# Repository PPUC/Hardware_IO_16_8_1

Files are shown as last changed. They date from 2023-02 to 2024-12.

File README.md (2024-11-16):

# Standard IO PCB for PPUC Project
This is the hardware for a standard IO card which was designed for the PPUC pinball project, but can be useful in other applications as well.
It is designed for being low cost and functional for experimental use.  
Not everything is tested nor does it fulfill EMC or any other specifications.  
Use at your own risk!
To make use of anything of this project a basic understanding of electronics and programming is necessary. Nothing of it is "plug and play". I'm surely not liable for any damage to assemblies, pinball machines or even persons.

## Picture of the Board
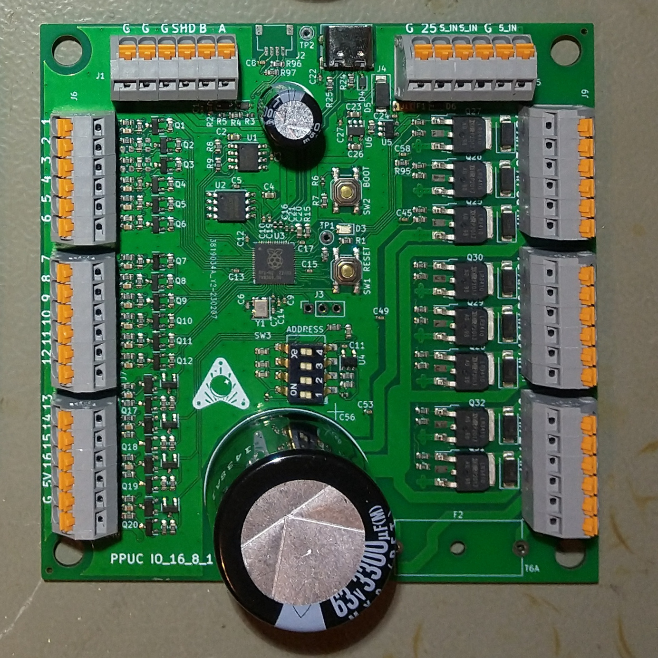
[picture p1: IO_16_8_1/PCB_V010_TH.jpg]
PCB Pic


## Name
IO_16_8_1 as it has 16 inputs, 8 outputs and one special output.  
Actually the inputs can also be used as outputs (see later in this document).

## Power Supply
The IO card must be supplied by 5 V (+-0.5 V) for logic and inputs. Additionally nominal 48 V for high power outputs. As these outputs are open drain, the voltage can actually be up to 60 V. In the circuit diagram the voltage is called 48 V.

## Controller
A RP2040 is used for it's cost/performance ratio. It is the same controller that is used in the Raspberry Pi Pico.

## Communication Interfaces
* RS_485: main communication interface for controlling outputs and scan inputs. Usually connected to a host interface like a PC or Raspberry Pi or similar.
* USB C: for programming, debug and flashing
* Serial Wire: alternative for programming, debug and flashing
* IIC: the PCB can be populated with an QWIIC connector (normally not mounted). This can be used for connecting to other PCBs or experimental use. It uses the same UART as for the RS485.
* UART, I2C, SPI: instead of using the input pins for inputs they can also be used as an additional interface (see docu of RP2040 for pins and function). Speed up to 10 kHz should be possible (100 kHz for In_2 and In_3).

## Switches (on board)
* Reset: hardware reset for controller (RP2040)
* Boot: if active the board connects to a PC like an USB stick. Usually used for programming the code into the flash memory on the board.
* DIP-switches: usually used to select an address for RS485 (16 combinations)

## Inputs (and low power outputs)
The 16 inputs are used for reading the state of an external switch. The switch is normally connected to ground (GND). Internally the input is pulled up to 5 V by a 10k resistor.

All inputs can also be used as signal-outputs (if programmed accordingly). The output is internally pulled up by a 10k resistor to 5 V. A higher voltage can be applied externally (max. 30 V) but be sure to have your hardware and software! setup correctly as no protection for damage is provided in that case. A maximum of 2 mA can be sinked/sourced.

The inputs In_2 and In_3 are designed for higher speed (100 kHz). The Pull-Up can be soldered to other pads to be pulled to 3,3 V (instead of 5 V). An input capacitance can be added (soldered) for better noise immunity but lower speed. Since version 1.0.1 the caps are soldered by default and must be removed if a high-speed serial connection is needed.

The input terminals can also be "miss"used for a switch matrix. To do that (no matter if used as coloum or row) the input resistor (330 Ohm) must be short cut (or replaced by a zero Ohm type). Background: the 330 Ohm resistor protects the circuit if the terminal is used as an output and accidently a short cut is done at the terminal. Unfortunately the low voltage value gets too high when used in a switch matrix (diode voltage plus voltage drop due to added up currents through the resistor). This happens when more switches are closed at the same time. Instead you could also use the specially designed PCB "Hardware_IO_16x8_matrix" for your switch matrix.

The inputs In_13 to In_16 have an additional open drain output transistor that allows higher currents in case of being used as an output (up to 3 A at 25 °C ambient temperature). The outputs are internally pulled up by a 10k resistor to 5 V. A higher voltage (max. 30 V) can be applied externally but be sure to have your hardware and software! setup correctly as no protection for damage is provided in that case. Please be aware that the default state (before software takes over control) is "on". 
If used as input In_13 to In_16 feature a memory (similar to a relay self-holding function). If the input has ever seen a low signal (e.g. switch closed to GND) it will stay that way until it gets an active high signal from the RP2040 (make the corresponding pin an output with signal "high" and then make it an input again). If this behavior is not wanted you can lift pin 3 of Q13 to Q16, then you have an input/output like e.g. terminal 1 with static behavior but no additional output power.

## High Power Outputs
There are 8 high power outputs available. Usually they are connected to pinball solenoids or flashers. A recovery diode for the solenoids is placed on the pcb, so no need for diodes at the coils. The outputs are open drain and drive currents up to 20 A with a load connected to a voltage of up to 60 V. Be aware that the current is limited by the fuse F2. It will blow within about 1 s at 20 A. You might use a 10 A fuse if necessary.

It's recommended to use 2 wires (back and forth) for each solenoid. That improves the EMC a lot.

## Special Output
One special output is available for high speed signals. The voltage is 5 V, it is a push pull output that can drive a current up to 8 mA. It can be used to e.g. control a WS2812 LED strip.

## Recommendations
* Connect only one Flipper to a pcb if possible. The advantage is, that all the energy of the big capacitor is available for the flipper, which is usually the solenoid with the highest current. If you have more flipper fingers than PCBs then spread the flipper solenoids as even as possible across the PCBs (e.g. if you have 6 flipper fingers it's better to connect 2 per board instead of all 6 at one board).
* Wire related switches and solenoids for fast flip devices (e.g. flipper, bumper, sling, kick back) to the same pcb. Then you can archive the shortest possible time lag between activating the switch and firing the solenoid.
* RS485 termination: short JP2 at the end of the RS485 bus. There should also be a 120 Ohm resistor at the beginning of the bus (e.g. USB to RS485 adapter).
* RS485 biasing: short JP1 and JP3 exactly once at any point of the RS485 bus. Only do this if no resistors are installed on the USB to RS485 adapter. 
* It's recommended to use flipper coils for higher voltage (like 40 - 50 V) as they draw less current. Since Version 1.1.1 low resistance coils (designed for 24 V) should work as well. You should also change the fuse F2 to 10 A for that application.
* If the MOSFETs on the high power outputs are not available (or you want to use the big player brands) here are some alternatives (I haven't tested any of them, but they should work according to their specification): GL40N10A4 (seems to be the same as NCE0140KA), RD3P200SNFRA, NVD6824NL, IPD90N10S4L-06, LSGG10R085W3

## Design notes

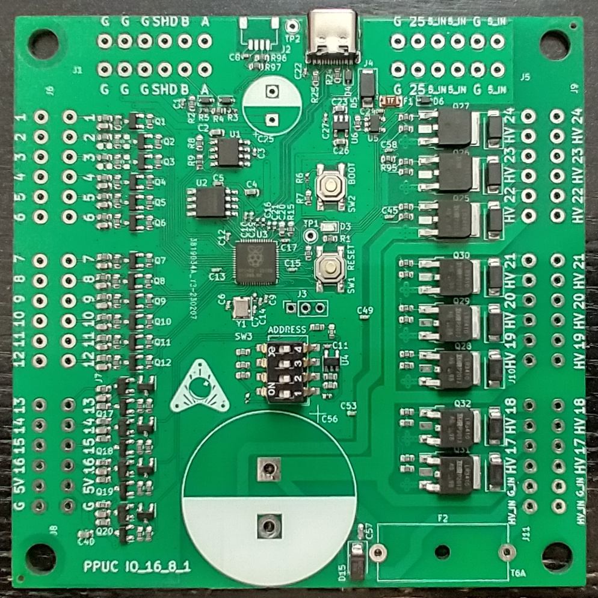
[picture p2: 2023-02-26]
IO_16_8_1/PCB_V010_SMD.jpg

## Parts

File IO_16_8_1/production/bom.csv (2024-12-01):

Designator | Footprint | Quantity | Value | LCSC Part #
C1, C10, C11, C12, C13, C14, C15, C17, C19, C22, C24, C27, C3, C45, C49, C5, C53, C58, C8, C9 | 0402 | 20 | 100n
C16, C21 | 0402 | 2 | 1u
C2, C20, C23, C26, C4, C40 | 0603 | 6 | 10u
C25 | CP_Elec_6.3x5.4 | 1 | 100µ 16V
C28, C29, C30, C31, C32, C33, C34, C35, C36, C37, C38, C39, C41, C42, C43, C44 | 0603 | 16 | 470p
C56 | CP_Radial_D30.0mm_P10.00mm_SnapIn | 1 | 3300µ 63V
C57 | 0603 | 1 | 100n 50V
C6, C7 | 0402 | 2 | 27pF
D1, D2 | D_SOD-323 | 2 | SD15
D10, D11, D12, D13, D14, D7, D8, D9 | D_SMA | 8 | MRA4004T3G
D15 | D_SMA | 1 | SMAJ60
D16, D4 | D_SOD-323 | 2 | 1A
D3 | 0805 | 1 | LED gn
D5 | D_SMA | 1 | SMAJ5.0
D6 | D_SOD-323 | 1 | SD05
F2 | Fuseholder_Cylinder-5x20mm_Schurter_0031_8201_Horizontal_Open | 1 | T6A
J1, J10, J11, J5, J6, J7, J8, J9 | Terminal_Block_RTMPin | 8 | Conn_01x06
J4 | USB_C_Receptacle_XKB_U262-16XN-4BVC11 | 1 | USB_C_Receptacle_USB2.0
JP1, JP2, JP3 | PinHeader_1x02_P2.54mm_Vertical | 3 | Jumper_2_Open
Q1, Q10, Q11, Q12, Q17, Q18, Q19, Q2, Q20, Q21, Q22, Q23, Q24, Q3, Q4, Q5, Q6, Q7, Q8, Q9 | SOT-23 | 20 | 2N7002
Q13, Q14, Q15, Q16 | SOT-23 | 4 | AO3400A
Q25, Q26, Q27, Q28, Q29, Q30, Q31, Q32 | TO-252-3_TabPin4 | 8 | NCE0140KA
R1, R26, R33, R36, R37, R38, R39, R42, R43, R44, R51, R52, R53, R54, R55, R56, R57, R58, R59, R60, R61, R62, R63, R64, R65, R66, R7, R71, R72, R73, R74, R75, R76, R77, R78, R79, R8, R80, R81, R85, R86, R87, R91, R92, R96, R97 | 0603 | 46 | 10k
R10, R11 | 0402 | 2 | 27
R12, R16, R20, R6 | 0402 | 4 | 1k
R13 | 0603 | 1 | 33k
R14, R18, R19, R23 | 0603 | 4 | 2k
R15, R2, R82, R83, R84, R88, R89, R90, R93, R94, R95 | 0603 | 11 | 100R
R17 | 0603 | 1 | 5k
R21 | 0603 | 1 | 470
R22, R34, R35, R40, R41 | 0603 | 5 | 3k
R24, R25 | 0603 | 2 | 5k1
R27, R28, R29, R30, R31, R32, R45, R46, R47, R48, R49, R50, R67, R68, R69, R70 | 0603 | 16 | 330
R3, R5 | 0402 | 2 | 620
R4 | 0603 | 1 | 120R
R9 | 0603 | 1 | 0
SW1 | SW_SPST_SKQG_WithStem | 1 | Reset
SW2 | SW_SPST_SKQG_WithStem | 1 | Boot
SW3 | SW_DIP_SPSTx04_Slide_6.7x11.72mm_W8.61mm_P2.54mm_LowProfile | 1 | ADDRESS
U1 | SOIC-8_3.9x4.9mm_P1.27mm | 1 | ADM3483
U2 | SOIC-8_5.23x5.23mm_P1.27mm | 1 | W25Q128JVSIQ
U3 | QFN-56-1EP_7x7mm_P0.4mm_EP3.2x3.2mm | 1 | RP2040
U4 | SOT-23-5 | 1 | LMV321
U5 | SOT-23-5 | 1 | SN74AHCT1G125
U6 | SOT-23-5 | 1 | AP2112K-3.3
Y1 | Crystal_SMD_3225-4Pin_3.2x2.5mm | 1 | 12MHz,18pF

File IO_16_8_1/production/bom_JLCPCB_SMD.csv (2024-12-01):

Designator | Footprint | Quantity | Value | LCSC Part #
C1, C10, C11, C12, C13, C14, C15, C17, C19, C22, C24, C27, C3, C45, C49, C5, C53, C58, C8, C9 | 0402 | 20 | 100n | C1525
C16, C21 | 0402 | 2 | 1u | C52923
C2, C20, C23, C26, C4, C40 | 0603 | 6 | 10u | C19702
C25 | CP_Elec_6.3x5.4 | 1 | 100µ 16V | C37308
C28, C29, C30, C31, C32, C33, C34, C35, C36, C37, C38, C39, C41, C42, C43, C44 | 0603 | 14 | 470p | C1620
C57 | 0603 | 1 | 100n 50V | C14663
C6, C7 | 0402 | 2 | 27pF | C1557
D1, D2 | D_SOD-323 | 2 | SD15 | C502529
D10, D11, D12, D13, D14, D7, D8, D9 | D_SMA | 8 | MRA4004T3G | C433394
D15 | D_SMA | 1 | SMAJ60 | C779057
D16, D4 | D_SOD-323 | 2 | 1A | C191023
D3 | 0805 | 1 | LED gn | C2297
D5 | D_SMA | 1 | SMAJ5.0 | C2925443
D6 | D_SOD-323 | 1 | SD05 | C2972756
J4 | USB_C_Receptacle_XKB_U262-16XN-4BVC11 | 1 | USB_C_Receptacle_USB2.0 | C709357
Q1, Q10, Q11, Q12, Q17, Q18, Q19, Q2, Q20, Q21, Q22, Q23, Q24, Q3, Q4, Q5, Q6, Q7, Q8, Q9 | SOT-23 | 20 | 2N7002 | C8545
Q13, Q14, Q15, Q16 | SOT-23 | 4 | AO3400A | C20917
Q25, Q26, Q27, Q28, Q29, Q30, Q31, Q32 | TO-252-3_TabPin4 | 8 | NCE0140KA | C194346
R1, R26, R33, R36, R37, R38, R39, R42, R43, R44, R51, R52, R53, R54, R55, R56, R57, R58, R59, R60, R61, R62, R63, R64, R65, R66, R7, R71, R72, R73, R74, R75, R76, R77, R78, R79, R8, R80, R81, R85, R86, R87, R91, R92, R96, R97 | 0603 | 46 | 10k | C25804
R10, R11 | 0402 | 2 | 27 | C138021
R12, R16, R20, R6 | 0402 | 4 | 1k | C11702
R13 | 0603 | 1 | 33k | C4216
R14, R18, R19, R23 | 0603 | 4 | 2k | C22975
R15, R2, R82, R83, R84, R88, R89, R90, R93, R94, R95 | 0603 | 11 | 100R | C22775
R17 | 0603 | 1 | 5k | C101077
R21 | 0603 | 1 | 470 | C23179
R22, R34, R35, R40, R41 | 0603 | 5 | 3k | C4211
R24, R25 | 0603 | 2 | 5k1 | C23186
R27, R28, R29, R30, R31, R32, R45, R46, R47, R48, R49, R50, R67, R68, R69, R70 | 0603 | 16 | 330 | C23138
R3, R5 | 0402 | 2 | 620 | C4961
R4 | 0603 | 1 | 120R | C22787
R9 | 0603 | 1 | 0 | C21189
SW1 | SW_SPST_SKQG_WithStem | 1 | Reset | C318884
SW2 | SW_SPST_SKQG_WithStem | 1 | Boot | C318884
SW3 | SW_DIP_SPSTx04_Slide_6.7x11.72mm_W8.61mm_P2.54mm_LowProfile | 1 | ADDRESS | C54950
U1 | SOIC-8_3.9x4.9mm_P1.27mm | 1 | ADM3483 | C609792
U2 | SOIC-8_5.23x5.23mm_P1.27mm | 1 | W25Q128JVSIQ | C97521
U3 | QFN-56-1EP_7x7mm_P0.4mm_EP3.2x3.2mm | 1 | RP2040 | C2040
U4 | SOT-23-5 | 1 | LMV321 | C7972
U5 | SOT-23-5 | 1 | SN74AHCT1G125 | C7484
U6 | SOT-23-5 | 1 | AP2112K-3.3 | C51118
Y1 | Crystal_SMD_3225-4Pin_3.2x2.5mm | 1 | 12MHz,18pF | C9002

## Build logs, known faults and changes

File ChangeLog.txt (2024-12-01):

2024-12-01  foenich

	Corrected silkscreen printing on J1 and J8
	No extra version released as schematic and function is not affected and nobody ever used V1.1.1 yet

2024-11-16  foenich

	Released Version 1.1.1
	Updated MOSFETS for power outputs (more current at low UGS)
		
	* changed type of Q25-Q32 (same package, no change in layout)

2024-10-04  foenich

	Released Version 1.1.0
	Jumpers for RS485 bias and termination. Adjusted bias resistors.
	Prevented current from USB to 5V_IN.
	+5V no longer at terminal, only internal supply
	More terminals for A and B.
	Smaller Cap for +5V
	
	* removed F1 (as +5V is no loger at a terminal)
	* inserted D16
	* changed J8, pin 5 from +5V to GND
	* changed J1, pin 4 from GND to A and pin 5 from GND to B
	* inserted JP1 to JP3
	* changed C25 from 1000µ-throuhole to 100µ-SMD
	* changed R3 and R5 form 1k to 620 Ohm (worst case for 16 nodes (Rin=12k) and 120 Ohm at beginning and end)

2023-10-21  foenich

	Released Version 1.0.1
	Changed default placement for capacitors at IN_2 and IN_3
	
	* set C29 and C30 to mount

2023-10-21  foenich

	Released Version 1.0.0
	Correct geometry for impedance controlled traces for USB
	
	* changed USB-wire witdh and reduced distance to GND
	* changed versioning to x.y.z (major.functional change.bugfix)

2023-03-07  foenich

	Correct voltage for addresses 0 to 7

	* changed R17 to 5k

2023-02-25  foenich

	Released initial Version 0.10

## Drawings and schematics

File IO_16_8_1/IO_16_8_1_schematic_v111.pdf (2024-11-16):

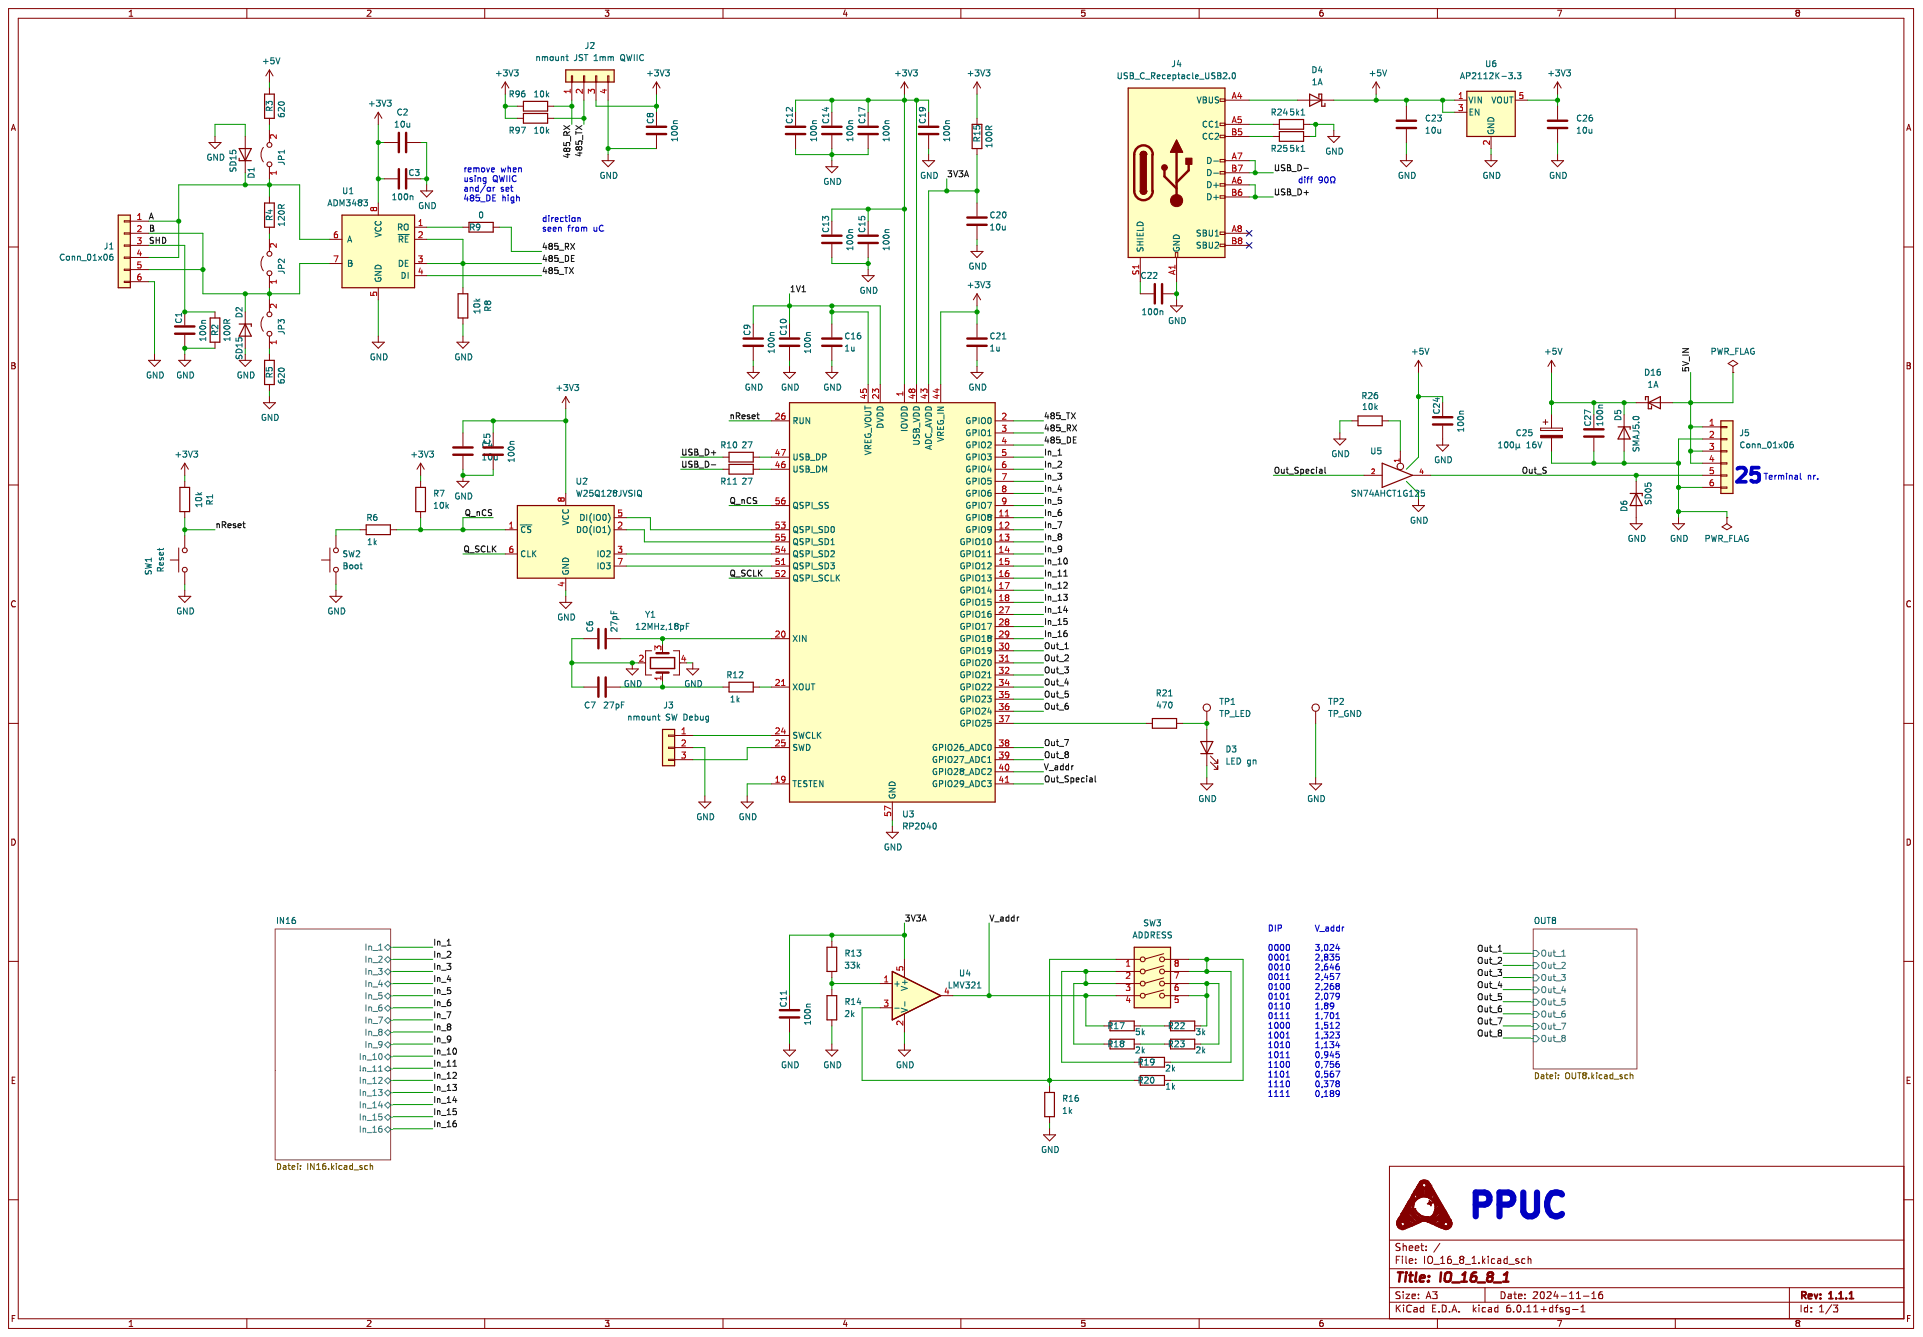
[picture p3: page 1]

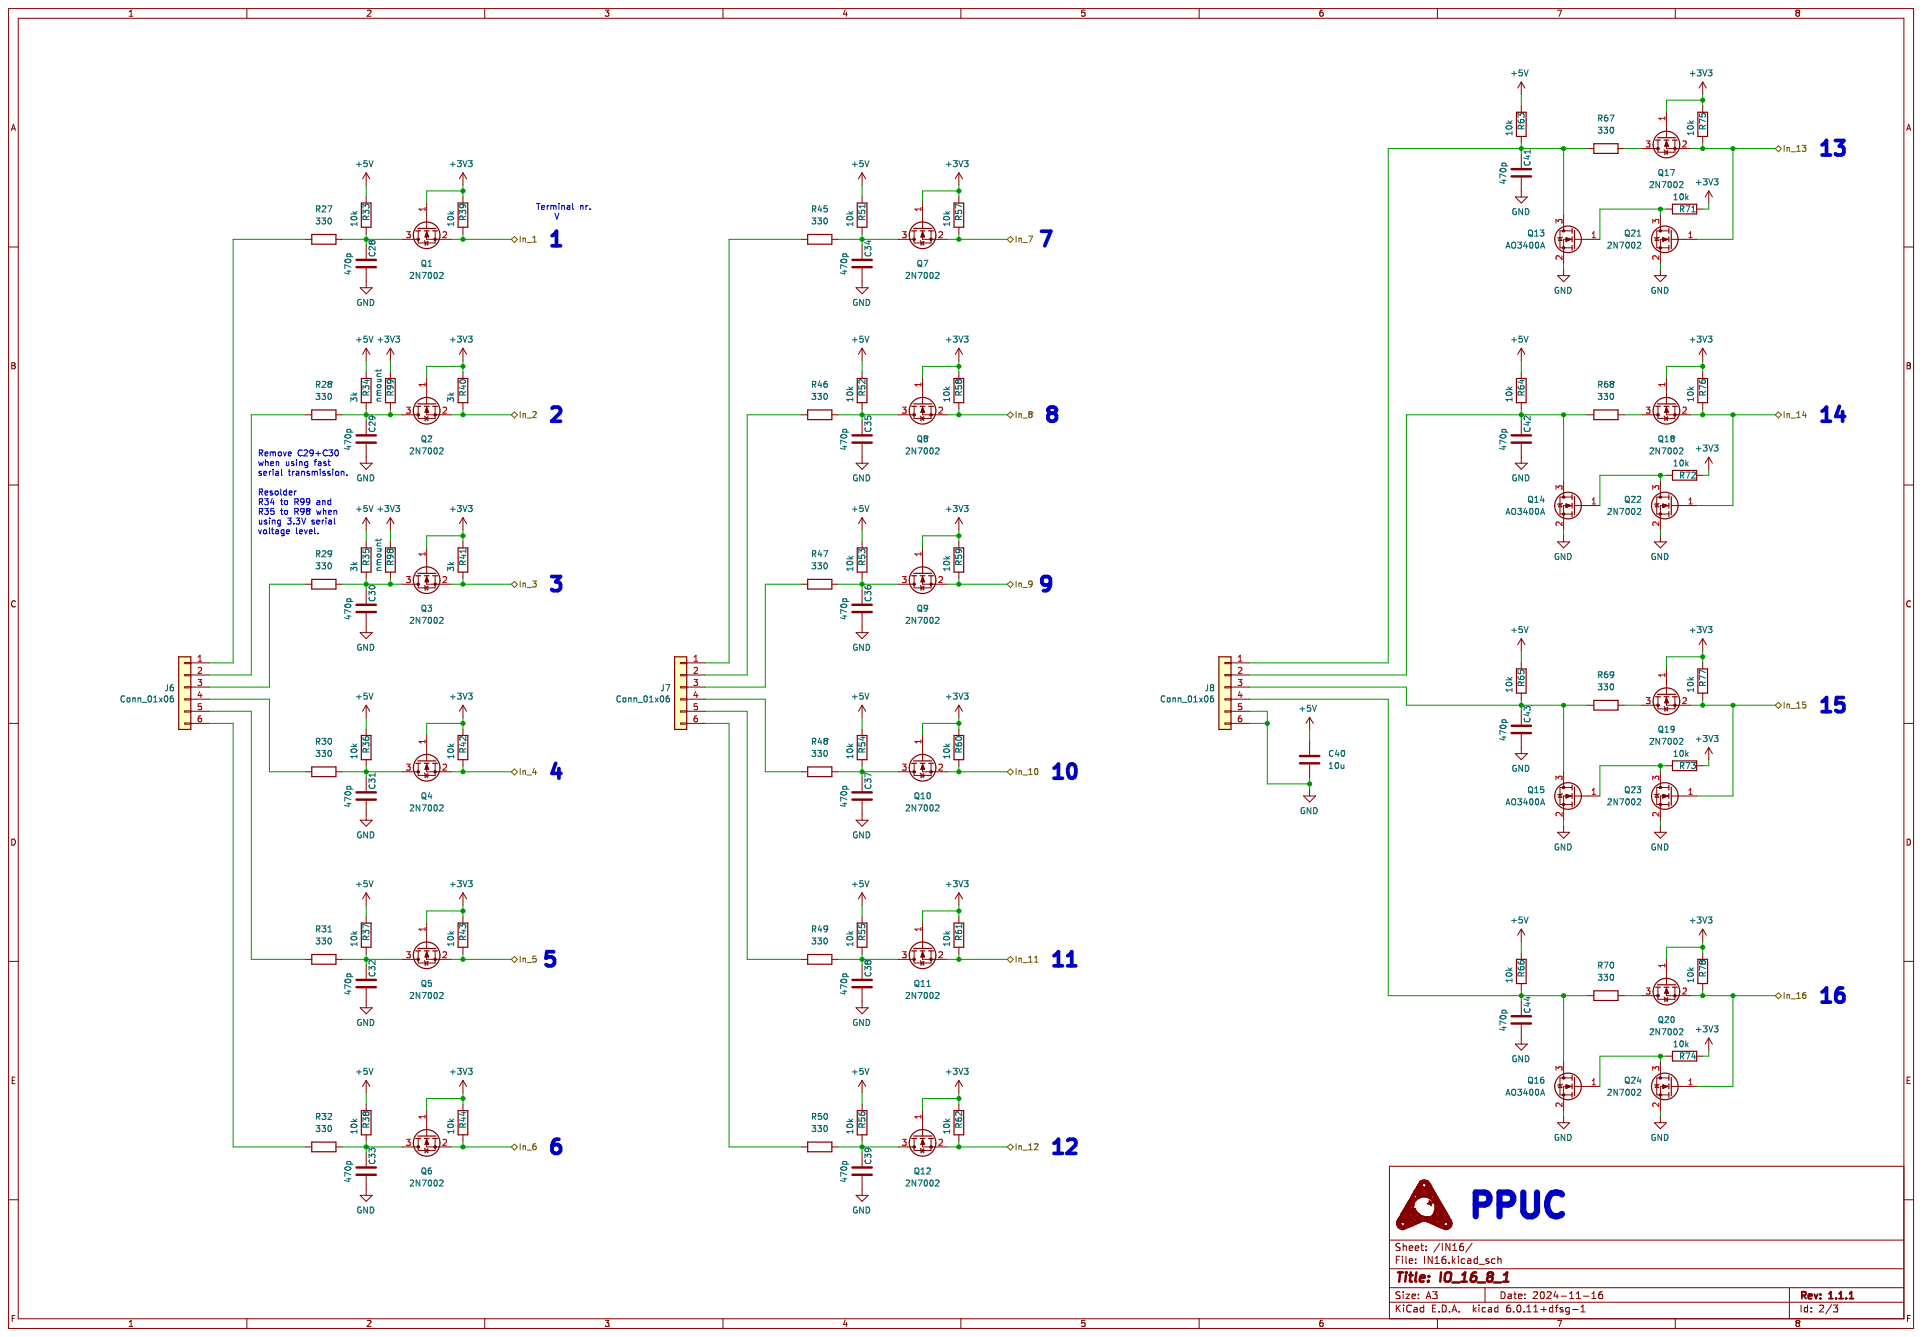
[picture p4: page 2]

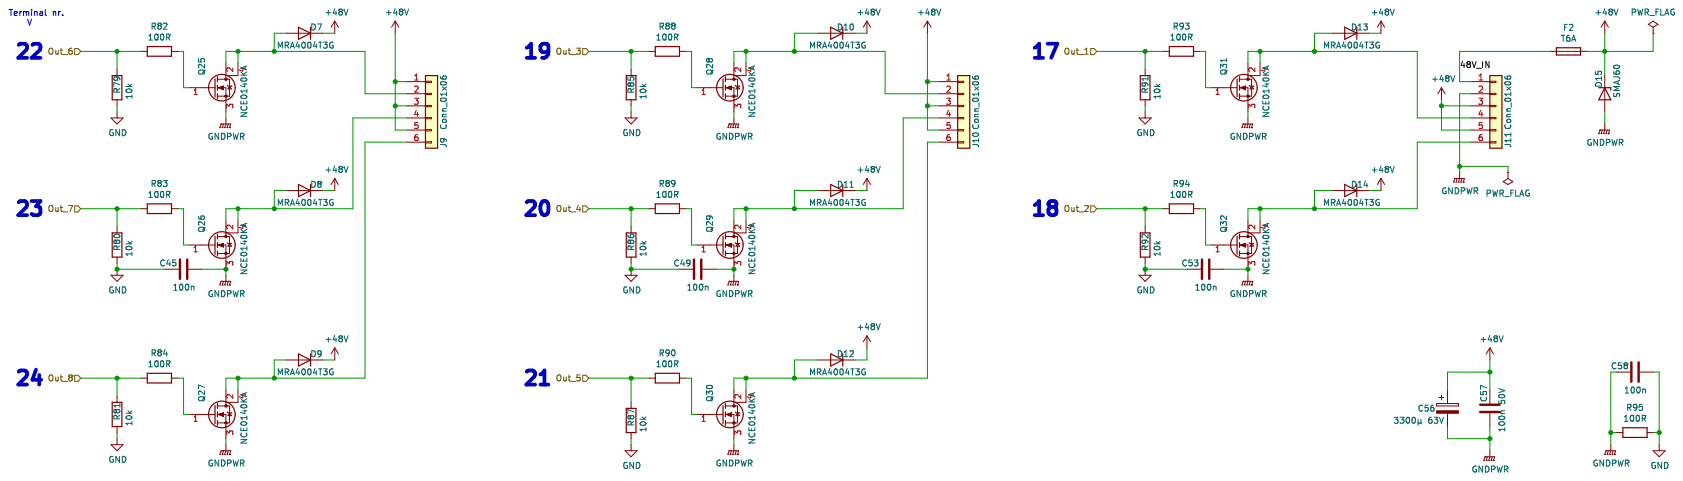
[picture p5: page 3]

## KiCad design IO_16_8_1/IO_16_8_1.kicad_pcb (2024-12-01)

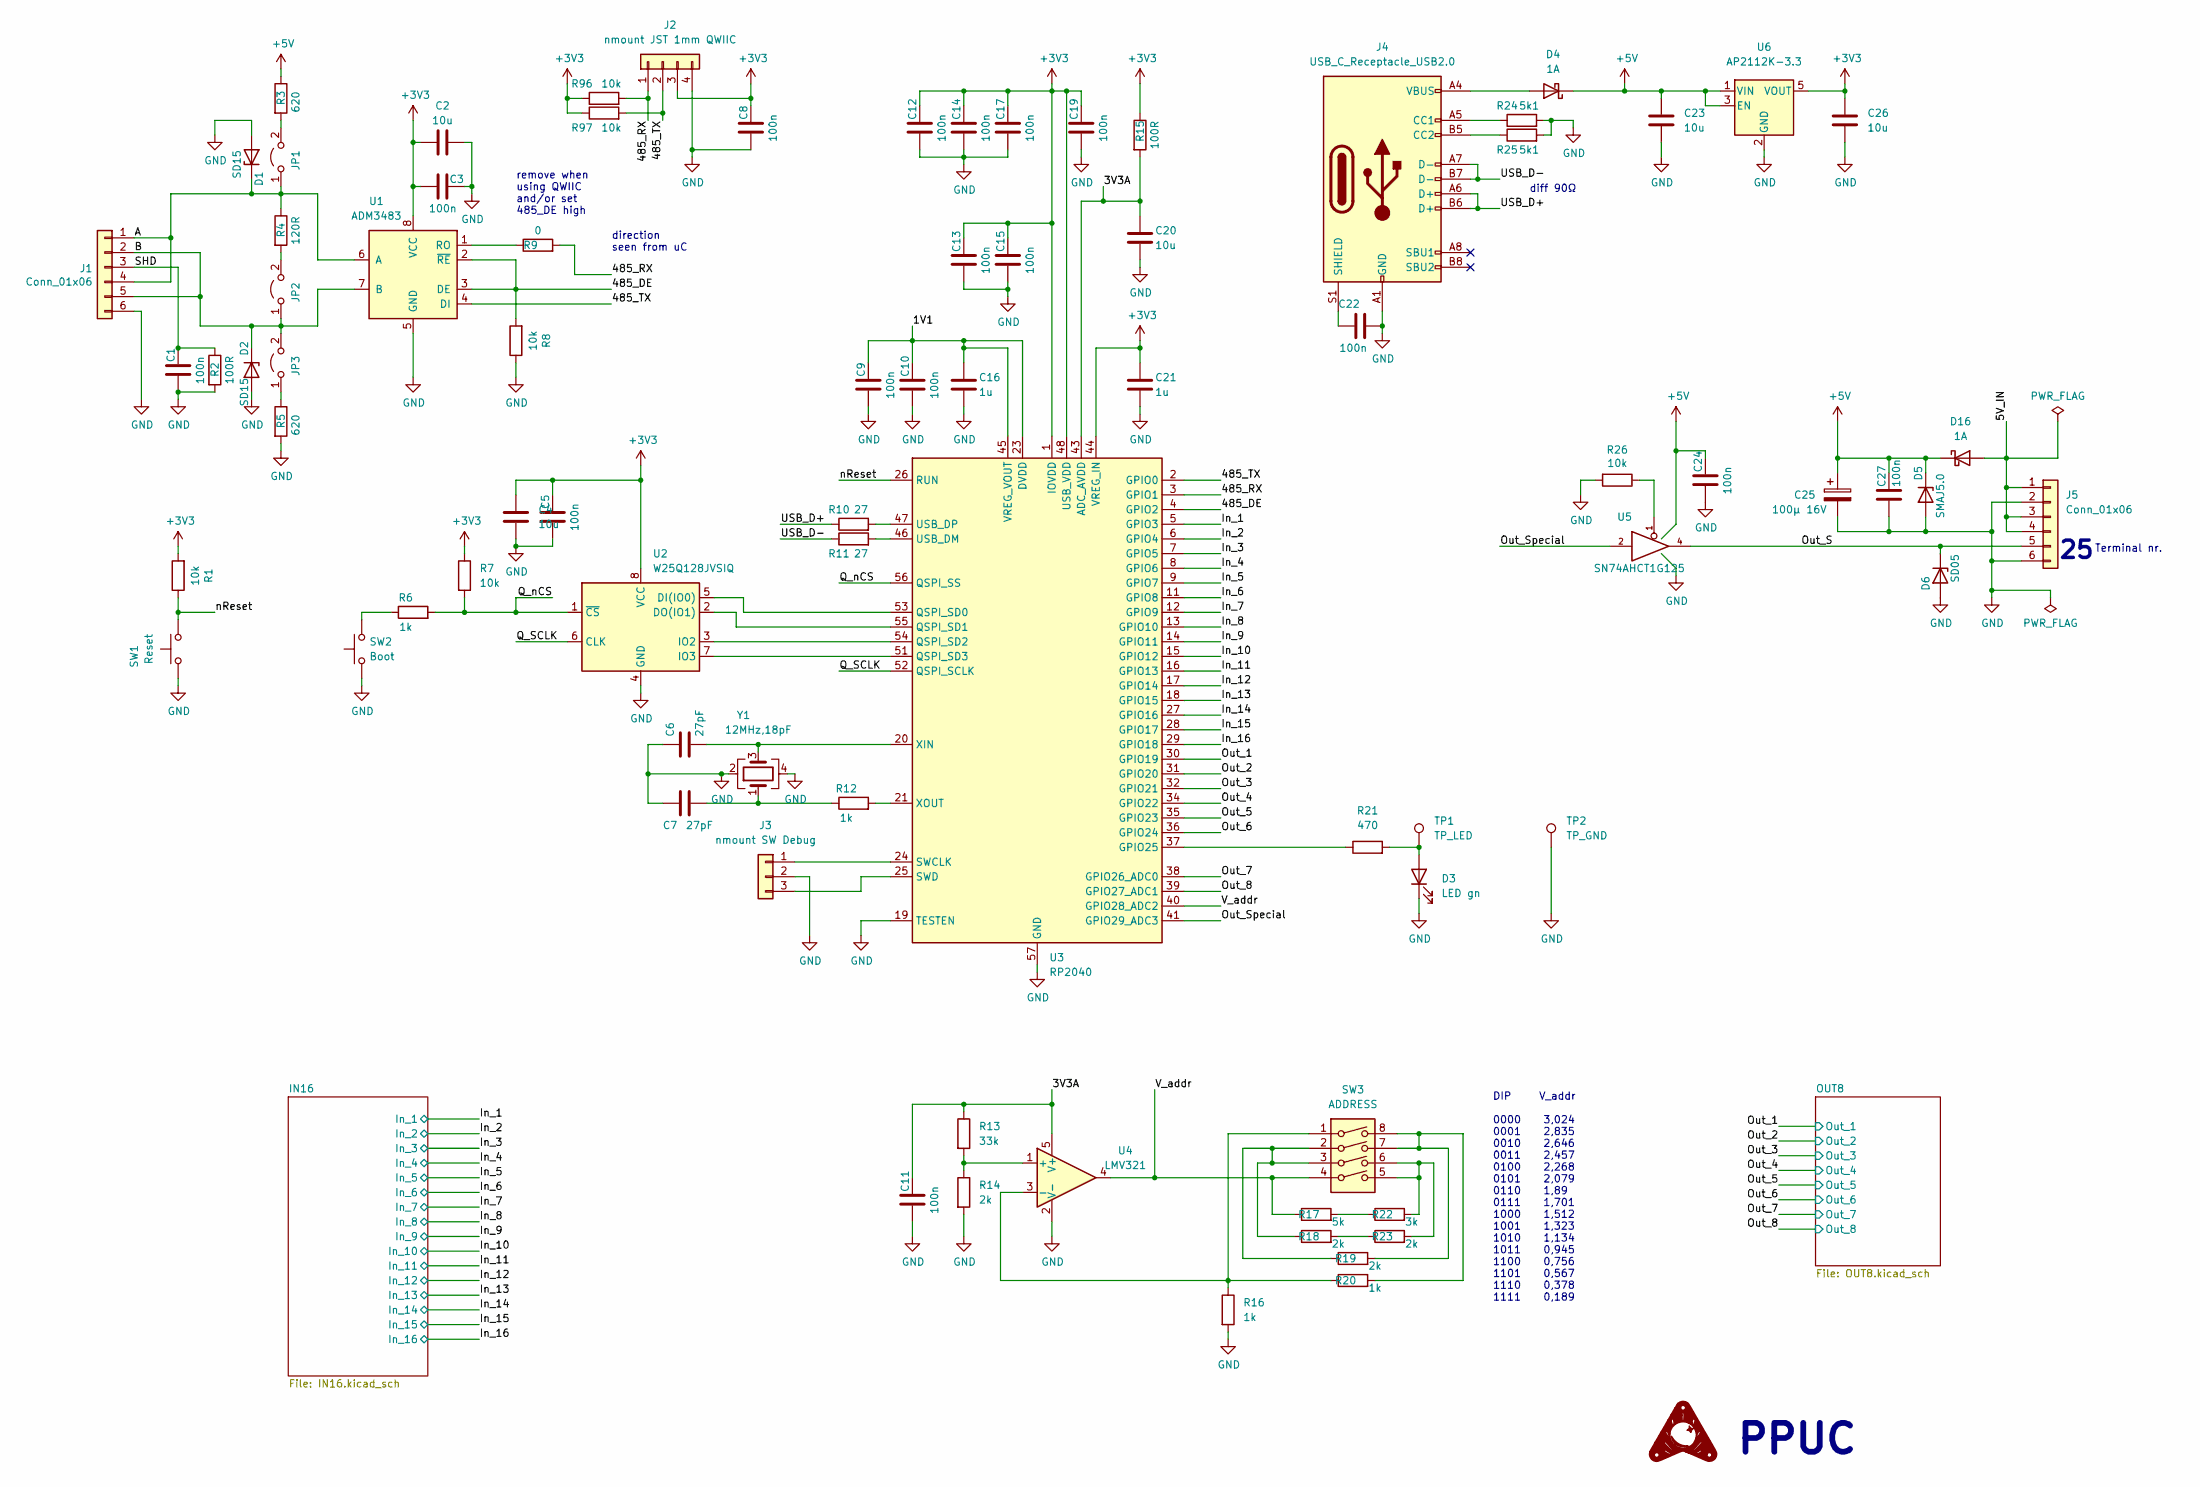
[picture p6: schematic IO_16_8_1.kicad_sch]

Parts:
C1, C3, C5, C8, C9, C10, C11, C12, C13, C14, C15, C17, C19, C22, C24, C27: 100n; C_0402_1005Metric
C2, C4, C20, C23, C26: 10u; C_0603_1608Metric
C6, C7: 27pF; C_0402_1005Metric
C16, C21: 1u; C_0402_1005Metric
C25: 100µ 16V; CP_Elec_6.3x5.4; JLCPCB Rotation Offset 180
D1, D2: SD15; D_SOD-323
D3: LED gn; LED_0805_2012Metric
D4, D16: 1A; D_SOD-323
D5: SMAJ5.0; D_SMA
D6: SD05; D_SOD-323
J1, J5: Conn_01x06; Terminal_Block_RTMPin
J2: nmount JST 1mm QWIIC; JST_SH_SM04B-SRSS-TB_1x04-1MP_P1.00mm_Horizontal
J3: nmount SW Debug; PinSocket_1x03_P2.54mm_Vertical
J4: USB_C_Receptacle_USB2.0; USB_C_Receptacle_XKB_U262-16XN-4BVC11
JP1, JP2, JP3: Jumper_2_Open; PinHeader_1x02_P2.54mm_Vertical
R1, R7, R8, R26, R96, R97: 10k; R_0603_1608Metric
R2, R15: 100R; R_0603_1608Metric
R3, R5: 620; R_0402_1005Metric
R4: 120R; R_0603_1608Metric
R6, R12, R16, R20: 1k; R_0402_1005Metric
R9: 0; R_0603_1608Metric
R10, R11: 27; R_0402_1005Metric
R13: 33k; R_0603_1608Metric
R14, R18, R19, R23: 2k; R_0603_1608Metric
R17: 5k; R_0603_1608Metric
R21: 470; R_0603_1608Metric
R22: 3k; R_0603_1608Metric
R24, R25: 5k1; R_0603_1608Metric
SW1: Reset; SW_SPST_SKQG_WithStem
SW2: Boot; SW_SPST_SKQG_WithStem
SW3: ADDRESS; SW_DIP_SPSTx04_Slide_6.7x11.72mm_W8.61mm_P2.54mm_LowProfile; JLCPCB Rotation Offset 90
TP1: TP_LED; Pin_D1.0mm_L10.0mm
TP2: TP_GND; Pin_D1.0mm_L10.0mm
U1: ADM3483; SOIC-8_3.9x4.9mm_P1.27mm
U2: W25Q128JVSIQ; SOIC-8_5.23x5.23mm_P1.27mm
U3: RP2040; QFN-56-1EP_7x7mm_P0.4mm_EP3.2x3.2mm; JLCPCB Rotation Offset -90
U4: LMV321; SOT-23-5
U5: SN74AHCT1G125; SOT-23-5
U6: AP2112K-3.3; SOT-23-5; JLCPCB Rotation Offset 90
Y1: 12MHz,18pF; Crystal_SMD_3225-4Pin_3.2x2.5mm

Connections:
+3V3: C2.1, C3.1, C4.1, C5.1, C8.1, C12.1, C13.1, C14.1, C15.1, C17.1, C19.1, C21.1, C26.1, J2.3, R1.2, R7.1, R15.1, R96.1, R97.1, U1.8 (VCC), U2.8 (VCC), U3.1 (IOVDD), U3.10 (IOVDD), U3.22 (IOVDD), U3.33 (IOVDD), U3.42 (IOVDD), U3.44 (VREG_IN), U3.48 (USB_VDD), U3.49 (IOVDD), U6.5 (VOUT); also elsewhere on the board
+5V: C23.1, C24.1, C25.1, C27.1, D4.1 (K), D5.1 (K), D16.1 (K), R3.1, U5.5 (VCC), U6.1 (VIN), U6.3 (EN); also elsewhere on the board
/1V1: C9.1, C10.1, C16.1, U3.23 (DVDD), U3.45 (VREG_VOUT), U3.50 (DVDD)
/3V3A: C11.1, C20.1, R13.1, R15.2, U3.43 (ADC_AVDD), U4.5 (V+)
/485_DE: R8.2, U1.2 (~RE), U1.3 (DE), U3.4 (GPIO2)
/485_RX: J2.1, R9.2, R96.2, U3.3 (GPIO1)
/485_TX: J2.2, R97.2, U1.4 (DI), U3.2 (GPIO0)
/A: D1.1 (K), J1.1, J1.4, JP1.1 (A), R4.1, U1.6 (A)
/B: D2.1 (K), J1.2, J1.5, JP2.1 (A), JP3.2 (B), U1.7 (B)
/In_1: U3.5 (GPIO3); also elsewhere on the board
/In_2: U3.6 (GPIO4); also elsewhere on the board
/In_3: U3.7 (GPIO5); also elsewhere on the board
/In_4: U3.8 (GPIO6); also elsewhere on the board
/In_5: U3.9 (GPIO7); also elsewhere on the board
/In_6: U3.11 (GPIO8); also elsewhere on the board
/In_7: U3.12 (GPIO9); also elsewhere on the board
/In_8: U3.13 (GPIO10); also elsewhere on the board
/In_9: U3.14 (GPIO11); also elsewhere on the board
/In_10: U3.15 (GPIO12); also elsewhere on the board
/In_11: U3.16 (GPIO13); also elsewhere on the board
/In_12: U3.17 (GPIO14); also elsewhere on the board
/In_13: U3.18 (GPIO15); also elsewhere on the board
/In_14: U3.27 (GPIO16); also elsewhere on the board
/In_15: U3.28 (GPIO17); also elsewhere on the board
/In_16: U3.29 (GPIO18); also elsewhere on the board
/Out_1: U3.30 (GPIO19); also elsewhere on the board
/Out_2: U3.31 (GPIO20); also elsewhere on the board
/Out_3: U3.32 (GPIO21); also elsewhere on the board
/Out_4: U3.34 (GPIO22); also elsewhere on the board
/Out_5: U3.35 (GPIO23); also elsewhere on the board
/Out_6: U3.36 (GPIO24); also elsewhere on the board
/Out_7: U3.38 (GPIO26_ADC0); also elsewhere on the board
/Out_8: U3.39 (GPIO27_ADC1); also elsewhere on the board
/Out_S: D6.1 (K), J5.5, U5.4
/Out_Special: U3.41 (GPIO29_ADC3), U5.2
/Q_SCLK: U2.6 (CLK), U3.52 (QSPI_SCLK)
/Q_nCS: R6.2, R7.2, U2.1 (~CS), U3.56 (QSPI_SS)
/SHD: C1.1, J1.3, R2.1
/USB_D+: J4.A6 (D+), J4.B6 (D+), R10.1
/USB_D-: J4.A7 (D-), J4.B7 (D-), R11.1
/V_addr: R17.1, SW3.4, U3.40 (GPIO28_ADC2), U4.4
/nReset: R1.1, SW1.2, U3.26 (RUN)
unnamed: C6.2, U3.20 (XIN), Y1.3
unnamed: C7.2, R12.1, Y1.1
unnamed: C22.1, J4.S1 (SHIELD)
unnamed: D3.2 (A), R21.2, TP1.1
unnamed: D4.2 (A), J4.A4 (VBUS), J4.A9 (VBUS), J4.B4 (VBUS), J4.B9 (VBUS)
unnamed: J3.1, U3.24 (SWCLK)
unnamed: J3.3, U3.25 (SWD)
unnamed: J4.A5 (CC1), R24.1
unnamed: J4.B5 (CC2), R25.1
unnamed: JP1.2 (B), R3.2
unnamed: JP2.2 (B), R4.2
unnamed: JP3.1 (A), R5.1
unnamed: R6.1, SW2.2
unnamed: R9.1, U1.1 (RO)
unnamed: R10.2, U3.47 (USB_DP)
unnamed: R11.2, U3.46 (USB_DM)
unnamed: R12.2, U3.21 (XOUT)
unnamed: R13.2, R14.1, U4.1 (+)
unnamed: R16.1, R20.1, SW3.1, U4.3 (-)
unnamed: R17.2, R22.1
unnamed: R18.1, R19.1, SW3.2, SW3.3
unnamed: R18.2, R23.1
unnamed: R19.2, R20.2, SW3.7, SW3.8
unnamed: R21.1, U3.37 (GPIO25)
unnamed: R22.2, R23.2, SW3.5, SW3.6
unnamed: R26.1, U5.1
unnamed: U2.2 (DO(IO1)), U3.55 (QSPI_SD1)
unnamed: U2.3 (IO2), U3.54 (QSPI_SD2)
unnamed: U2.5 (DI(IO0)), U3.53 (QSPI_SD0)
unnamed: U2.7 (IO3), U3.51 (QSPI_SD3)

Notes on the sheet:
diff 90Ω
DIP V_addr 0000 3,024 0001 2,835 0010 2,646 0011 2,457 0100 2,268 0101 2,079 0110 1,89 0111 1,701 1000 1,512 1001 1,323 1010 1,134 1011 0,945 1100 0,756 1101 0,567 1110 0,378 1111 0,189
direction seen from uC
Terminal nr.
PPUC
remove when using QWIIC and/or set 485_DE high

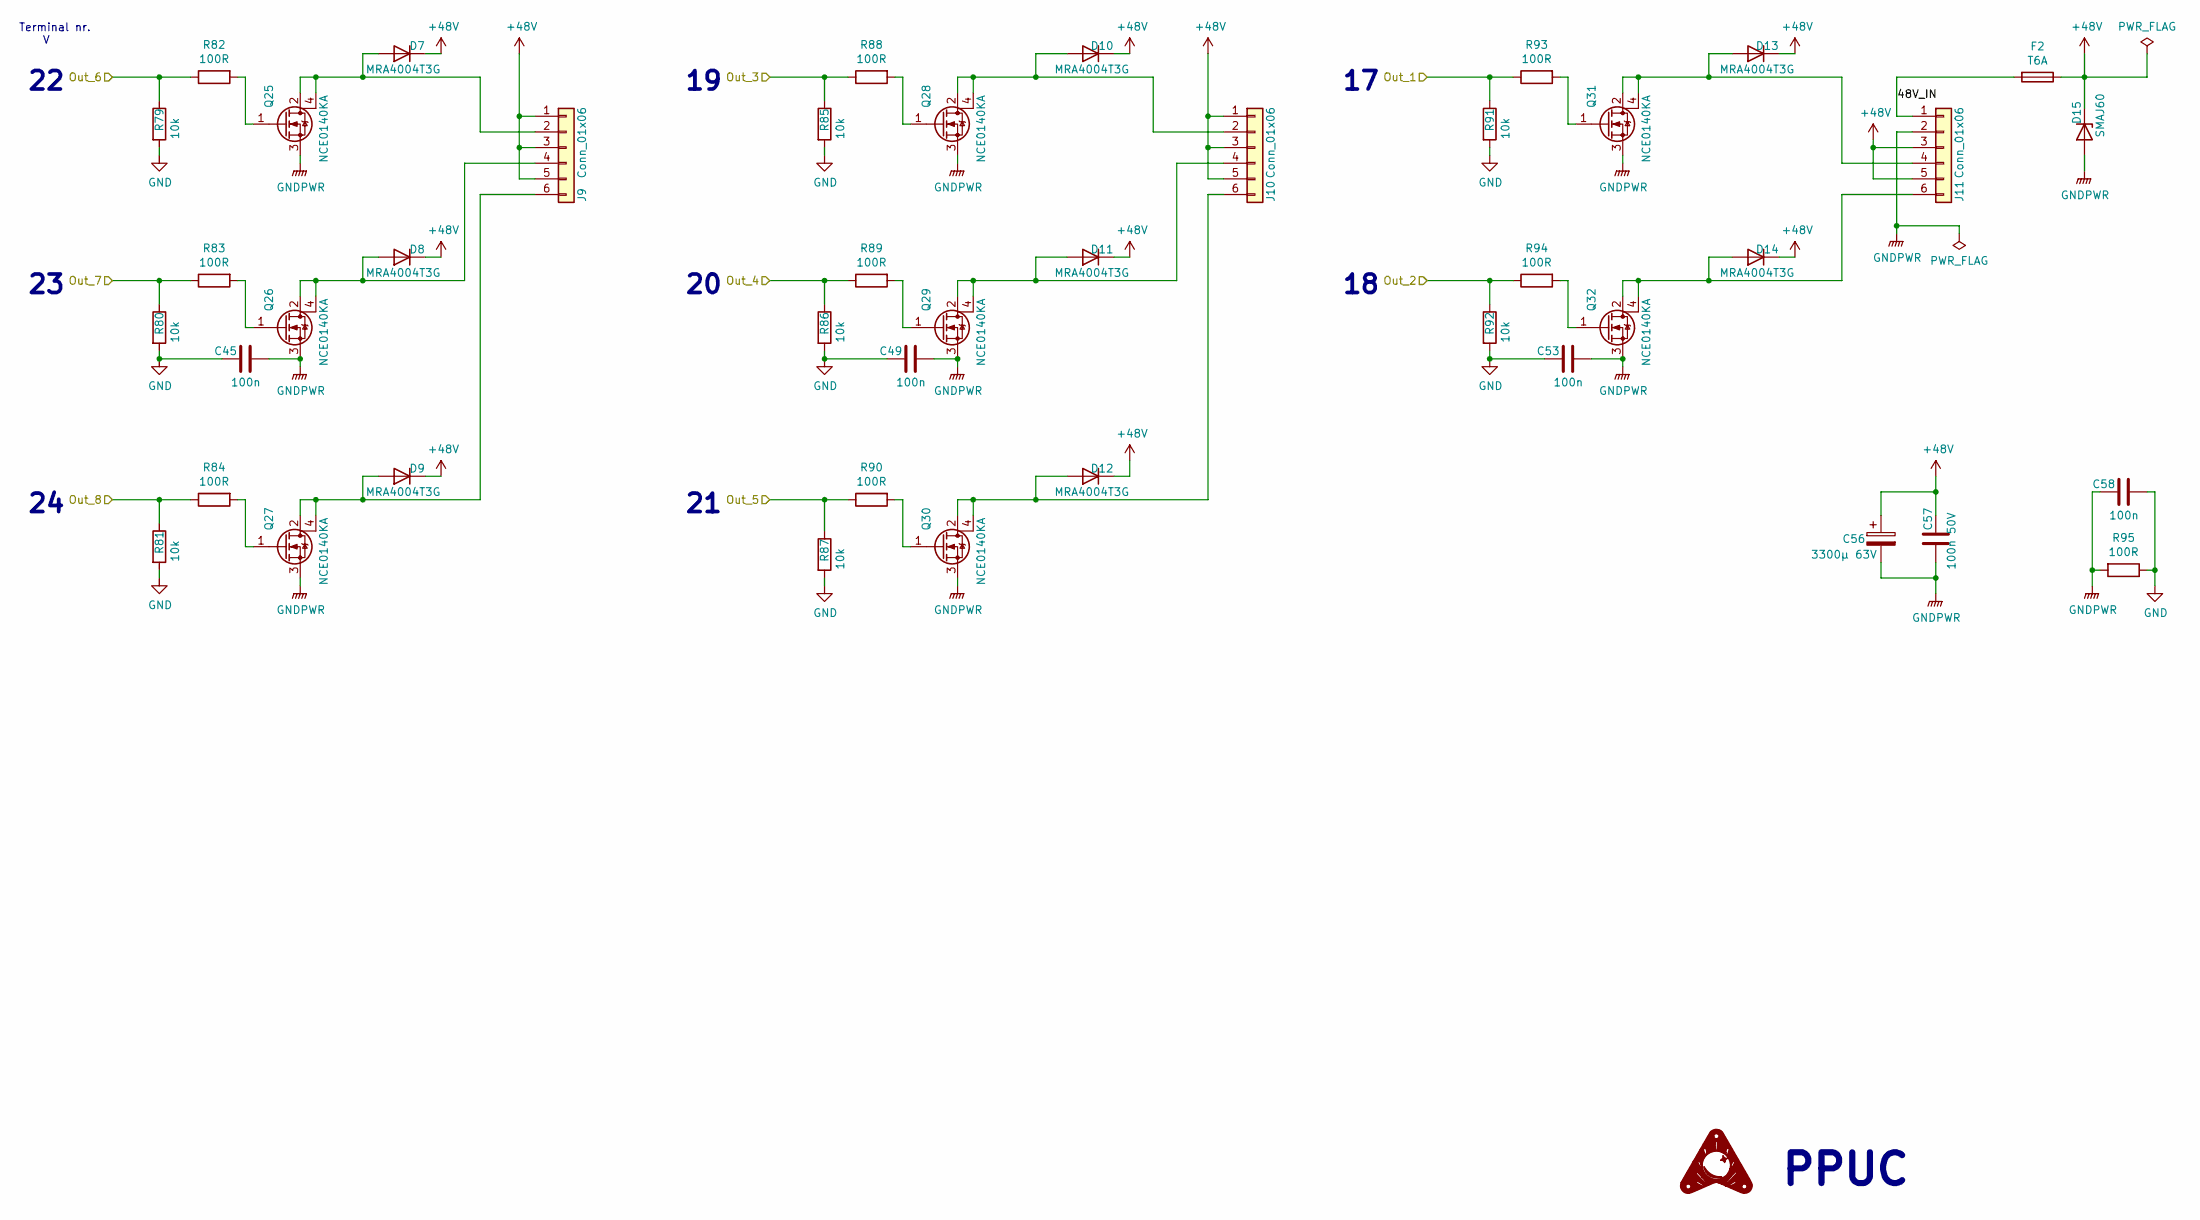
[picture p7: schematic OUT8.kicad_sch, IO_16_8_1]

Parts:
C45, C49, C53, C58: 100n; C_0402_1005Metric
C56: 3300µ 63V; CP_Radial_D30.0mm_P10.00mm_SnapIn
C57: 100n 50V; C_0603_1608Metric
D7, D8, D9, D10, D11, D12, D13, D14: MRA4004T3G; D_SMA
D15: SMAJ60; D_SMA
F2: T6A; Fuseholder_Cylinder-5x20mm_Schurter_0031_8201_Horizontal_Op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
J9, J10, J11: Conn_01x06; Terminal_Block_RTMPin
Q25, Q26, Q27, Q28, Q29, Q30, Q31, Q32: NCE0140KA; TO-252-3_TabPin4
R79, R80, R81, R85, R86, R87, R91, R92: 10k; R_0603_1608Metric
R82, R83, R84, R88, R89, R90, R93, R94, R95: 100R; R_0603_1608Metric

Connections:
/OUT8/48V_IN: F2.2, J11.1
/Out_1: R91.1, R93.1; also elsewhere on the board
/Out_2: R92.1, R94.1; also elsewhere on the board
/Out_3: R85.1, R88.1; also elsewhere on the board
/Out_4: R86.1, R89.1; also elsewhere on the board
/Out_5: R87.1, R90.1; also elsewhere on the board
/Out_6: R79.1, R82.1; also elsewhere on the board
/Out_7: R80.1, R83.1; also elsewhere on the board
/Out_8: R81.1, R84.1; also elsewhere on the board
unnamed: D7.2 (A), J9.2, Q25.2 (D), Q25.4 (D)
unnamed: D8.2 (A), J9.4, Q26.2 (D), Q26.4 (D)
unnamed: D9.2 (A), J9.6, Q27.2 (D), Q27.4 (D)
unnamed: D10.2 (A), J10.2, Q28.2 (D), Q28.4 (D)
unnamed: D11.2 (A), J10.4, Q29.2 (D), Q29.4 (D)
unnamed: D12.2 (A), J10.6, Q30.2 (D), Q30.4 (D)
unnamed: D13.2 (A), J11.4, Q31.2 (D), Q31.4 (D)
unnamed: D14.2 (A), J11.6, Q32.2 (D), Q32.4 (D)
unnamed: Q25.1 (G), R82.2
unnamed: Q26.1 (G), R83.2
unnamed: Q27.1 (G), R84.2
unnamed: Q28.1 (G), R88.2
unnamed: Q29.1 (G), R89.2
unnamed: Q30.1 (G), R90.2
unnamed: Q31.1 (G), R93.2
unnamed: Q32.1 (G), R94.2

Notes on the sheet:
Terminal nr. V
PPUC

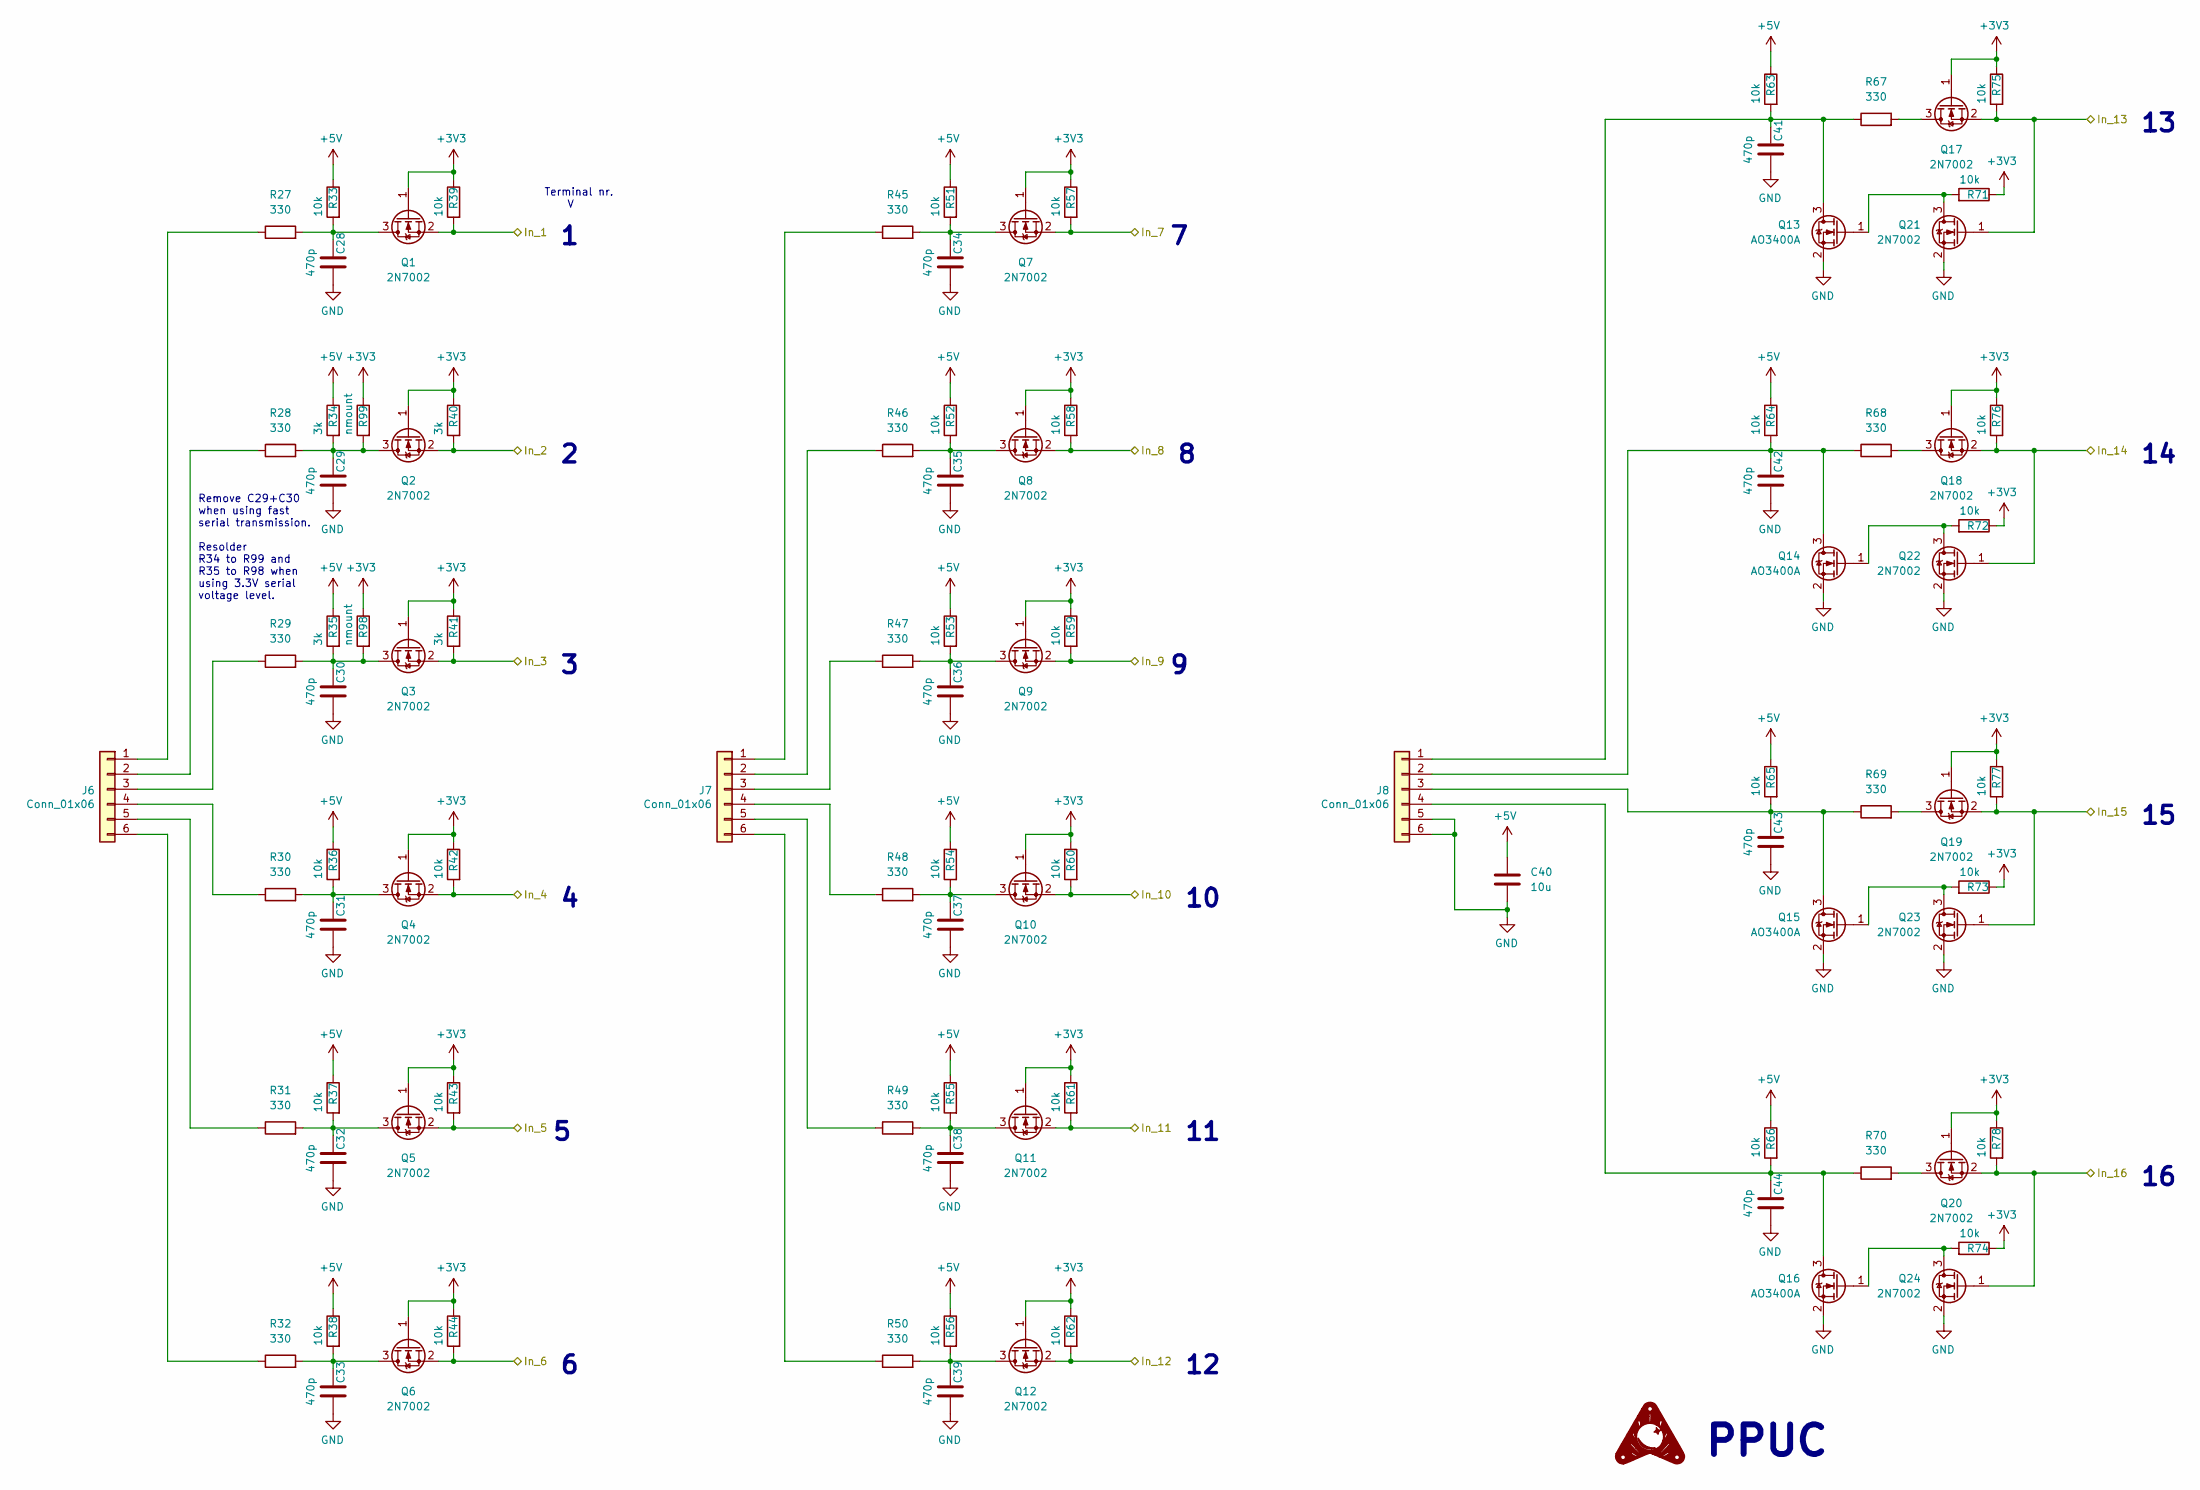
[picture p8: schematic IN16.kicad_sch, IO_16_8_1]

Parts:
C28, C29, C30, C31, C32, C33, C34, C35, C36, C37, C38, C39, C41, C42, C43, C44: 470p; C_0603_1608Metric
C40: 10u; C_0603_1608Metric
J6, J7, J8: Conn_01x06; Terminal_Block_RTMPin
Q1, Q2, Q3, Q4, Q5, Q6, Q7, Q8, Q9, Q10, Q11, Q12, Q17, Q18, Q19, Q20, Q21, Q22, Q23, Q24: 2N7002; SOT-23
Q13, Q14, Q15, Q16: AO3400A; SOT-23
R27, R28, R29, R30, R31, R32, R45, R46, R47, R48, R49, R50, R67, R68, R69, R70: 330; R_0603_1608Metric
R33, R36, R37, R38, R39, R42, R43, R44, R51, R52, R53, R54, R55, R56, R57, R58, R59, R60, R61, R62, R63, R64, R65, R66, R71, R72, R73, R74, R75, R76, R77, R78: 10k; R_0603_1608Metric
R34, R35, R40, R41: 3k; R_0603_1608Metric
R98, R99: nmount; R_0603_1608Metric

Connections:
+3V3: Q1.1 (G), Q2.1 (G), Q3.1 (G), Q4.1 (G), Q5.1 (G), Q6.1 (G), Q7.1 (G), Q8.1 (G), Q9.1 (G), Q10.1 (G), Q11.1 (G), Q12.1 (G), Q17.1 (G), Q18.1 (G), Q19.1 (G), Q20.1 (G), R39.1, R40.1, R41.1, R42.1, R43.1, R44.1, R57.1, R58.1, R59.1, R60.1, R61.1, R62.1, R71.1, R72.1, R73.1, R74.1, R75.1, R76.1, R77.1, R78.1, R98.1, R99.1; also elsewhere on the board
+5V: C40.1, R33.1, R34.1, R35.1, R36.1, R37.1, R38.1, R51.1, R52.1, R53.1, R54.1, R55.1, R56.1, R63.1, R64.1, R65.1, R66.1; also elsewhere on the board
/In_1: Q1.2 (S), R39.2; also elsewhere on the board
/In_2: Q2.2 (S), R40.2; also elsewhere on the board
/In_3: Q3.2 (S), R41.2; also elsewhere on the board
/In_4: Q4.2 (S), R42.2; also elsewhere on the board
/In_5: Q5.2 (S), R43.2; also elsewhere on the board
/In_6: Q6.2 (S), R44.2; also elsewhere on the board
/In_7: Q7.2 (S), R57.2; also elsewhere on the board
/In_8: Q8.2 (S), R58.2; also elsewhere on the board
/In_9: Q9.2 (S), R59.2; also elsewhere on the board
/In_10: Q10.2 (S), R60.2; also elsewhere on the board
/In_11: Q11.2 (S), R61.2; also elsewhere on the board
/In_12: Q12.2 (S), R62.2; also elsewhere on the board
/In_13: Q17.2 (S), Q21.1 (G), R75.2; also elsewhere on the board
/In_14: Q18.2 (S), Q22.1 (G), R76.2; also elsewhere on the board
/In_15: Q19.2 (S), Q23.1 (G), R77.2; also elsewhere on the board
/In_16: Q20.2 (S), Q24.1 (G), R78.2; also elsewhere on the board
unnamed: C28.1, Q1.3 (D), R27.2, R33.2
unnamed: C29.1, Q2.3 (D), R28.2, R34.2, R99.2
unnamed: C30.1, Q3.3 (D), R29.2, R35.2, R98.2
unnamed: C31.1, Q4.3 (D), R30.2, R36.2
unnamed: C32.1, Q5.3 (D), R31.2, R37.2
unnamed: C33.1, Q6.3 (D), R32.2, R38.2
unnamed: C34.1, Q7.3 (D), R45.2, R51.2
unnamed: C35.1, Q8.3 (D), R46.2, R52.2
unnamed: C36.1, Q9.3 (D), R47.2, R53.2
unnamed: C37.1, Q10.3 (D), R48.2, R54.2
unnamed: C38.1, Q11.3 (D), R49.2, R55.2
unnamed: C39.1, Q12.3 (D), R50.2, R56.2
unnamed: C41.1, J8.1, Q13.3 (D), R63.2, R67.1
unnamed: C42.1, J8.2, Q14.3 (D), R64.2, R68.1
unnamed: C43.1, J8.3, Q15.3 (D), R65.2, R69.1
unnamed: C44.1, J8.4, Q16.3 (D), R66.2, R70.1
unnamed: J6.1, R27.1
unnamed: J6.2, R28.1
unnamed: J6.3, R29.1
unnamed: J6.4, R30.1
unnamed: J6.5, R31.1
unnamed: J6.6, R32.1
unnamed: J7.1, R45.1
unnamed: J7.2, R46.1
unnamed: J7.3, R47.1
unnamed: J7.4, R48.1
unnamed: J7.5, R49.1
unnamed: J7.6, R50.1
unnamed: Q13.1 (G), Q21.3 (D), R71.2
unnamed: Q14.1 (G), Q22.3 (D), R72.2
unnamed: Q15.1 (G), Q23.3 (D), R73.2
unnamed: Q16.1 (G), Q24.3 (D), R74.2
unnamed: Q17.3 (D), R67.2
unnamed: Q18.3 (D), R68.2
unnamed: Q19.3 (D), R69.2
unnamed: Q20.3 (D), R70.2

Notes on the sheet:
PPUC
Remove C29+C30 when using fast serial transmission. Resolder R34 to R99 and R35 to R98 when using 3.3V serial voltage level.
Terminal nr. V

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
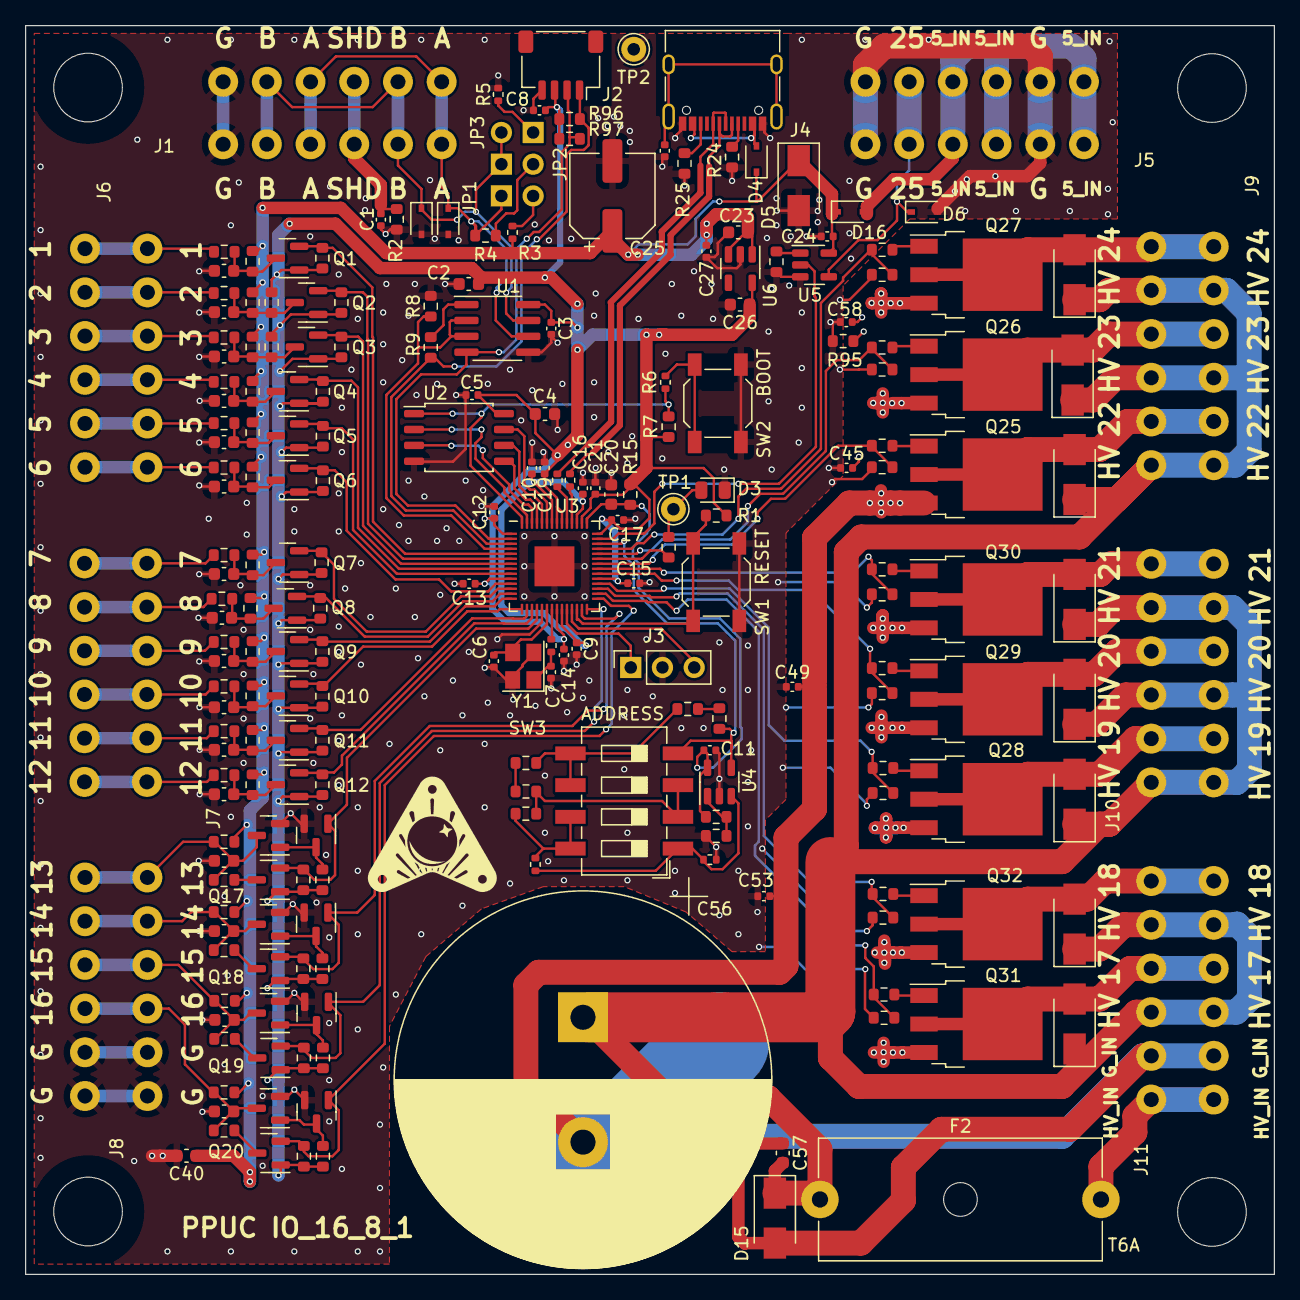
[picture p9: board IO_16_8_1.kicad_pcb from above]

Board: 2 copper layers, 100.0 x 100.0 mm, 223 parts (0 on the bottom side), 129 nets.

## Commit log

2022-12-11 initial version
    [IN16.kicad_sch, IO_16_8_1.kicad_pcb, IO_16_8_1.kicad_sch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]
2022-12-12 fixed typo QUIIC -> QWIIC
    [IO_16_8_1.kicad_sch]
2022-12-14 changed In_1, In_2
    [IN16.kicad_sch, IO_16_8_1.kicad_sch, OUT8.kicad_sch]
2022-12-18 different pins for RS485
    [IN16.kicad_sch, IO_16_8_1.kicad_sch]
2022-12-30 PCB init
    [IN16.kicad_sch, IO_16_8_1.kicad_pcb, IO_16_8_1.kicad_sch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]
2023-01-05 placed out
    [IN16.kicad_sch, IO_16_8_1.kicad_pcb, IO_16_8_1.kicad_sch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]
2023-01-06 placed logic
    [IO_16_8_1.kicad_pcb]
2023-01-10 smaller Cs
    [IO_16_8_1.kicad_pcb, IO_16_8_1.kicad_sch, OUT8.kicad_sch]
2023-01-17 1/2 routed
    [IO_16_8_1.kicad_pcb, IO_16_8_1.kicad_sch, OUT8.kicad_sch]
2023-03-07 changed R17
    [IO_16_8_1.kicad_pcb, IO_16_8_1.kicad_sch]
2024-03-27 prod. data
    [IO_16_8_1-B_Cu.gbl, IO_16_8_1-B_Mask.gbs, IO_16_8_1-B_Paste.gbp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]
2024-10-04 Release 1.1.0
    [IN16.kicad_sch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]
2024-11-16 changed MOSFETs
    [IN16.kicad_sch, IO_16_8_1.kicad_pcb, IO_16_8_1.kicad_sch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]
2024-12-01 added production data
    [IN16.kicad_sch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]
2024-12-01 corrected silk J1, J8
    [IO_16_8_1.kicad_pcb]
